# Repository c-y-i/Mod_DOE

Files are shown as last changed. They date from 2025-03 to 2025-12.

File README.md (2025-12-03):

# Mod_DOE
This GitHub repository is presented as supplementary material to the paper *Co-Optimization of Design and Manufacturing Parameters for Low-Cost Robotic Actuation*, authored by Gregory M. Campbell, Yi Cao, Hannah Escritor, Zihao Zhou, and Mark Yim. 

ArXiV to be uploaded here when created.

## **Description of the file structure**:

* Root files include .pkl files of tests for design paramaters chose by taguchi array (Taguchi_test_dict, taguchi_valve_dict) and Bayesian Optimization (BayzOp_test_dict, BO_valve_dict_High_lglg). It also includes the optimizations (BayZop_Running & BayZop_Valve) with associated utility functions (utils). It also includes the experimental scripts (Run_Gear_Experiment, Run_Valve_Experiment) with associated utility functions (Experiment_Utils). Finally, it includes .csv files of design parameters for Taguchi generated (Tag_d_params, valve_tag_d_params) and BO generated (d_params, valve_BO_d_params).

* BO_desings includes BO output design values for gear testing.

* Valve_designs includes BO output design values for valve testing.

* wolfrom includes theoretical gear design files used for parameter selection.

* CAD includes computer-aided design files for an example gear and valve mold

## Files and variables:

### **root**:

* BayZop_Running.ipynb: use Ax.dev to run Bayesian Optimization for gear parameter optimization.

* BayzOp_test_dict.pkl: 'pickle' file containing a dictionary of characterization test data for gear designs generated via Bayesian Optimization. Each 'key' contains design number: 'BO_##'. Each 'value' contains a list of [n] elements where each element represents a test. Each test element is a list of [2] elements, where each element represents a data stream. Each data element is a [m_i,2] vector in list form, where the first column represents time [ms] and the second column represents: dynamixel MX-28 torque activation [Element 0], current (mA) [Element 1]

* BayZop_Valve.ipynb: use Ax.dev to run Bayesian Optimization for valve parameter optimization.

* BO_valve_dict_High_lglg.pkl: 'pickle' file containing a dictionary of characterization test data for valve designs generated via Bayesian Optimization. Each 'key' contains information about the pressure level and pneumatic capcitor size, as well as design number: 'Prelim_High_lglg#'. Each 'value' contains a list of [n] elements where each element represents a test. Each test element is a list of [2] elements, where the first element is a [m,1] vector of time values [ms] and the second element is a list corresponding to a [2,m] vector of pressure values [kPa] where the first column represents pressure in the pre-valve pneumatic capacitor and the second column represents pressure in the post-valve pneumatic capacitor.

* d_params.csv: a comma-seperated-value file containing values relevant to CAD-work for gear designs generated via L32b Taguchi array. Wolfram gear design values provided are, in order: design number, number of teeth on sun gear, number of teeth on first part of planet gears, number of teeth on second part of planet gears, number of teeth on ring gear 2, profile shift coefficient for the sun gear, profile shift coefficient for the first part of planet gears, profile shift coefficient for the second part of planet gears, profile shift coefficient for ring gear 2, carrier radii [mm], gear thickness for all gears [mm].

* Experiment_Utils.py: utility functions to aid in valve / gear test experiments.

* Figure_Plotting.ipynb: plots and data analysis relevant to paper results.

* requirements.txt: a list of Python packages required for this code-base.

* Run_Gear_Experiment: functions for user-setup and activated of automated gear testing / data collection.

* Run_Valve_Experiment: functions for user-setup and activated of automated valve testing / data collection.

* Serial_Comms.py: utility functions for serial communication with dynamixel and ESP32.

* Tag_d_params.csv: comma-seperated-value file containing design parameter values and gear ratios for gear designs generated via L32b Taguchi array. Wolfram gear design values provided are, in order: design number, 3d-printer filament, lubricant, half the number of teeth on sun gear, number of teeth on ring gear 2, profile shift coefficient for the sun gear, profile shift coefficient for ring gear 2, clearance between teeth and roots of meshing gears [m], half the gear thickness for all gears [mm], offset integer affecting teeth and profile shift coefficient for planet 1, offset integer affecting teeth and profile shift coefficient  for planet 2, gear ratio of wolfram bilateral planetary gear.

* Taguchi_test_dict.pkl: 'pickle' file containing a dictionary of characterization test data for gear designs generated via L32b Taguchi array. Each 'key' contains design number: 'Taguchi_Design_#'. Each 'value' contains a list of [n] elements where each element represents a test. Each test element is a list of [2] elements, where each element represents a data stream. Each data element is a [2xm_i] vector in list form, where the first column represents time [ms] and the second column represents: dynamixel MX-28 torque activation [Element 0], current (mA) [Element 1]

* taguchi_valve_dict.pkl: 'pickle' file containing a dictionary of characterization test data for valve designs generated via L16b Taguchi array. Each 'key' contains information about the pressure level and pneumatic capcitor size, as well as design number: 'Prelim_High_lglg#'. Each 'value' contains a list of [n] elements where each element represents a test. Each test element is a list of [2] elements, where the first element is a [m,1] vector of time values [ms] and the second element is a list corresponding to a[2,m] vector of pressure values [kPa] where the first column represents pressure in the pre-valve pneumatic capacitor and the second column represents pressure in the post-valve pneumatic capacitor.

* utils.py: utility functions to aid in valve / gear analysis and Bayesian Optimization.

* valve_BO_d_params.csv: comma-seperated-value file containing design parameter values and test results for valve designs generated via Bayesian Optimization. Design values provided are, in order: design number, material (Ecoflex/Dragonskin silicone), valve thickness [mm], valve dome height [mm], cut length for slit in silicone valve [mm], cut geometry, test result for crack pressure [kPa], test result for steady-state pressure difference [kPa].

* valve_tag_d_params.csv: comma-seperated-value file containing design parameter values for valve designs generated via L16b Taguchi array. Design values provided are, in order: design number, material (Ecoflex/Dragonskin silicone), valve thickness [mm], valve dome height [mm], cut length for slit in silicone valve [mm], cut geometry, test result for crack pressure [kPa], test result for steady-state pressure difference [kPa].

* one_shots_d_params.csv: comma-seperated-value file containing design parameter values for valve designs generated via BO trained on 0: all Taguchi trials and 1: all Taguchi and BO trials. Design values provided are, in order: design number, material (Ecoflex/Dragonskin silicone), valve thickness [mm], valve dome height [mm], cut length for slit in silicone valve [mm], cut geometry, test result for crack pressure [kPa], test result for steady-state pressure difference [kPa].

### **BO_designs**: 

* BO_d_params.csv: a comma-seperated-value file containing values relevant to CAD-work for gear designs generated via Bayesian Optimization. Wolfram gear design values provided are, in order: design number, number of teeth on sun gear, number of teeth on first part of planet gears, number of teeth on second part of planet gears, number of teeth on ring gear 2, profile shift coefficient for the sun gear, profile shift coefficient for the first part of planet gears, profile shift coefficient for the second part of planet gears, profile shift coefficient for ring gear 2, carrier radii [mm], gear thickness for all gears [mm]. 

* BO_OneShot_d_vals.csv: a comma-seperated-value file containing values relevant to CAD-work for gear design generated via Bayesian Optimization from all Taguchi tests. Wolfram gear design values provided are, in order: design number, number of teeth on sun gear, number of teeth on first part of planet gears, number of teeth on second part of planet gears, number of teeth on ring gear 2, profile shift coefficient for the sun gear, profile shift coefficient for the first part of planet gears, profile shift coefficient for the second part of planet gears, profile shift coefficient for ring gear 2, carrier radii [mm], gear thickness for all gears [mm], clearance between teeth and roots of meshing gears [m], 3d-printer filament, lubricant.

* BO_OneShot_meta_vals.csv: comma-seperated-value file containing design parameter values and gear ratios for gear designs generated via Bayesian Optimization from all Taguchi tests. Wolfram gear design values provided are, in order: design number, 3d-printer filament, lubricant, half the number of teeth on sun gear, number of teeth on ring gear 2, profile shift coefficient for the sun gear, profile shift coefficient for ring gear 2, clearance between teeth and roots of meshing gears [m], half the gear thickness for all gears [mm], offset integer affecting teeth and profile shift coefficient for planet 1, offset integer affecting teeth and profile shift coefficient for planet 2, gear ratio of wolfram bilateral planetary gear.

* trial_[XX,YY]_d_vals.csv: comma-seperated-value file containing design parameter values and gear ratios for gear designs generated via Bayesian Optimization during acquisition that yielded design numbers XX and YY. Wolfram gear design values provided are, in order: design number, 3d-printer filament, lubricant, half the number of teeth on sun gear, number of teeth on ring gear 2, profile shift coefficient for the sun gear, profile shift coefficient for ring gear 2, clearance between teeth and roots of meshing gears [m], half the gear thickness for all gears [mm], offset integer affecting teeth and profile shift coefficient for planet 1, offset integer affecting teeth and profile shift coefficient for planet 2, gear ratio of wolfram bilateral planetary gear.

### **Valve_designs**: 

* valve_trial_[X].csv: comma-seperated-value file containing design parameter values for valve designs generated via Bayesian Optimization during acquisition that yielded design number X. Design values provided are, in order: design number, material (Ecoflex/Dragonskin silicone), cut geometry, valve thickness [mm], valve dome height [mm], cut length for slit in silicone valve [mm].

### **wolfrom**

This folder contains tools, scripts, and data for Wolfrom gearbox design and optimization.

* **gear_maker** - Gear Generator add-in for Fusion 360  
  - `gear_maker.py` - Source code for the add-in.  
  - `gear_maker.manifest` - Add-in metadata file required for Fusion 360 to run the script.  

* **config.json** - Parameter definitions and value ranges for gearbox generation.  

* **design_params.py** - Alternative method for generating design parameters for the Taguchi Array.  

* **cross_reference.py** - Post-processes results from `design_params.py` to create candidate designs for the Taguchi Array.  

* **gear_optimization_visualization.ipynb** - design space visualization for choosing relevant gear parameter inputs to L32b taguchi array.
  
### **CAD**

This folder contains printable parts and assemblies for the Wolfrom gearbox (Bayesian Optimization trial **BO22**) and the valve mold set (All-trials One-Shot).

#### [`gear_BO22`](./CAD/gear_BO22) - Wolfrom gearbox (BO trial 22)
Files here provide both individual STL parts for 3D printing and full assemblies for reference/CAD transfer.

* **STL parts (ready to print)**
  - `22_sun_12_0.7513_6.stl` - sun gear  
  - `22_planet_36_0.7854_28_*.stl` - two-stage planet gear (first and second segments)  
  - `22_ring2_76_0.1686_6.stl` - ring gear 2  
  - `ring1_90_6.stl` - ring gear 1  
  - `22_carrier2_20.7_6.stl` - planet carrier  

  *Naming note:* Filenames encode trial and key parameters (e.g., tooth counts, profile shift, thickness in mm).

* **Assemblies**
  - `BO_22_Gearbox.f3d` - Fusion 360 design file for the BO22 assembly, bearing & shaft parts included.
  - `BO_22_Gearbox.step` - neutral STEP export of the same assembly for use outside Fusion.

#### [`valve_ALL_OS`](./CAD/valve_ALL_OS) - Valve (All-trials One-Shot)
Parametric solids for the “one-shot” valve mold halves:

* `ALL_OS_f.SLDPRT` - **female** (cavity) half.  
* `ALL_OS_m.SLDPRT` - **male** (protruding/core) half.

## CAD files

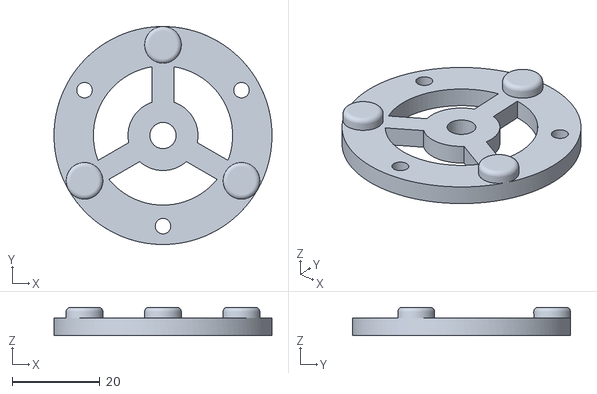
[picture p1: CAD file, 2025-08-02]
CAD/gear_BO22/22_carrier1_20.7_6.stl
49.8 x 49.8 x 6.50

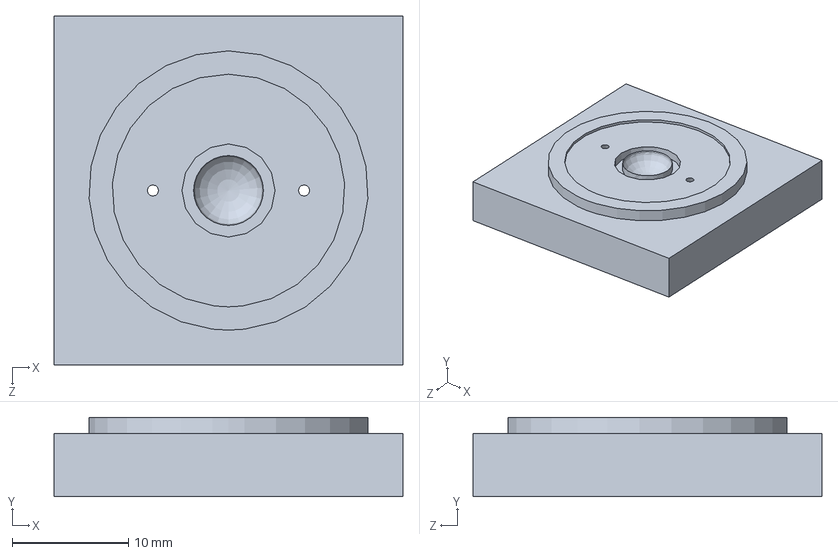
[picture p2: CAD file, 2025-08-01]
CAD/valve_ALL_OS/ALL_OS_f.SLDPRT
30.0 x 6.80 x 30.0 mm

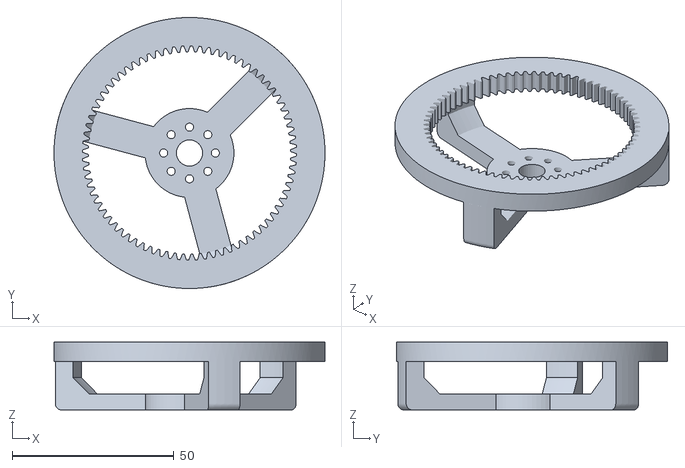
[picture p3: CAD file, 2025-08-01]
CAD/gear_BO22/22_ring2_76_0.1686_6.stl
83.8 x 83.8 x 21.0

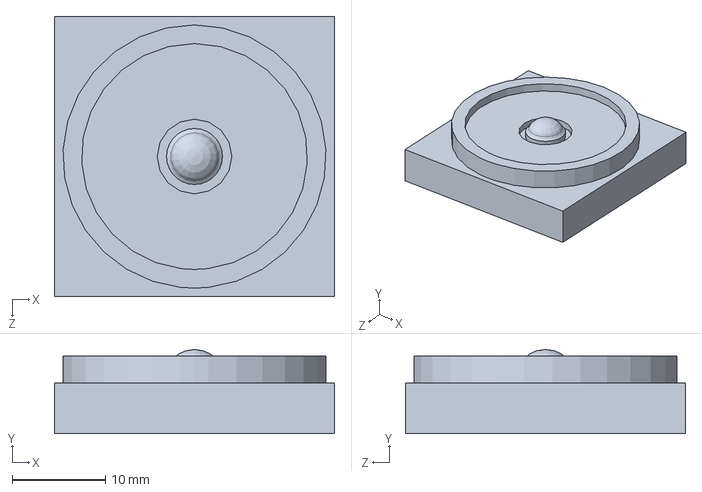
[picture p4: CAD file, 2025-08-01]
CAD/valve_ALL_OS/ALL_OS_m.SLDPRT
30.0 x 9.00 x 30.0 mm

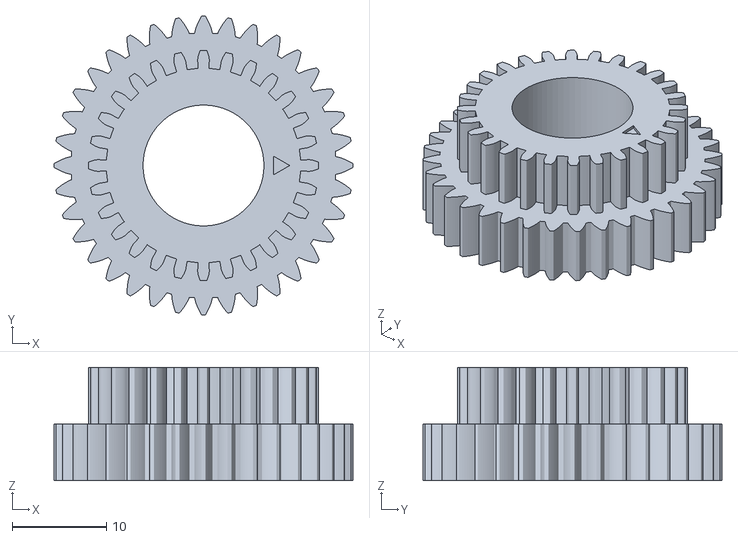
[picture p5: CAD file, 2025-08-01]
CAD/gear_BO22/22_planet_36_0.7854_28_-0.6001_6.stl
31.7 x 31.7 x 12.0

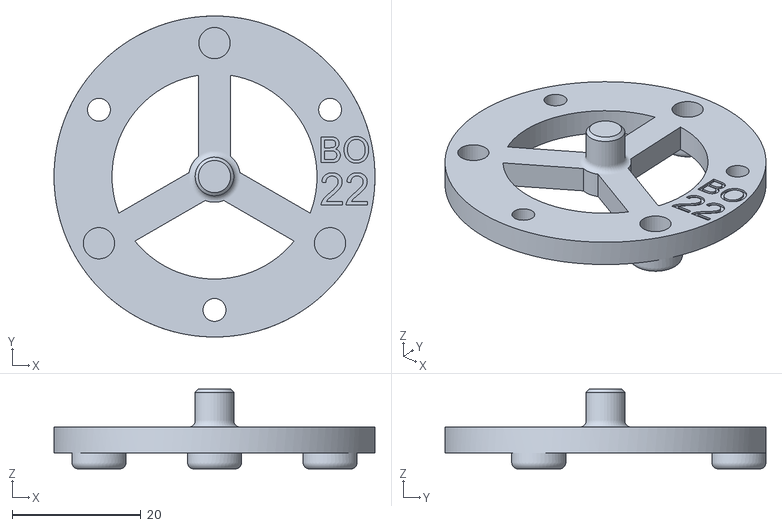
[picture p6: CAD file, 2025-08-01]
CAD/gear_BO22/22_carrier2_20.7_6.stl
49.8 x 49.8 x 12.4

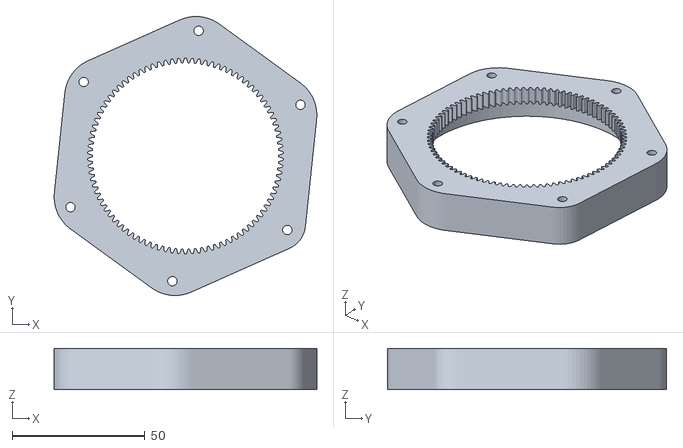
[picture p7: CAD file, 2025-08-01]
CAD/gear_BO22/ring1_90_6.stl
98.8 x 104.9 x 15.6

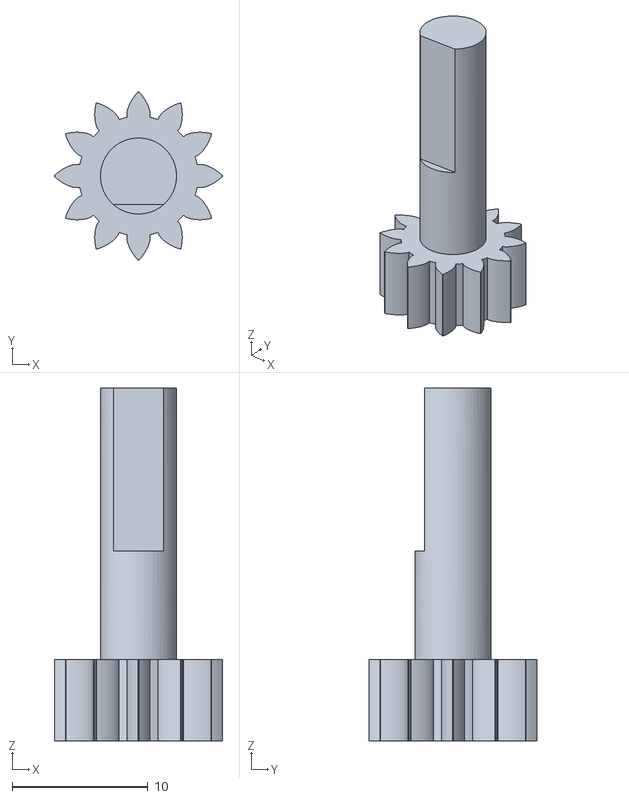
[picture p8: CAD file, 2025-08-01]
CAD/gear_BO22/22_sun_12_0.7513_6.stl
12.4 x 12.4 x 26.0

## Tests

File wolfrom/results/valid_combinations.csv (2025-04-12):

z_s | z_p1 | z_p2 | z_r2 | xs | xp1 | xp2 | xr2 | Ratio | eta_fwd | eta_bwd
10.0 | 39.0 | 29.0 | 76 | 0.6 | 0.07499999999999929 | 0.27732372741230193 | 0.8 | 83.72881355932206 | 0.6787387837036755 | 0.579254321904389
10.0 | 39.0 | 29.0 | 76 | 0.6 | 0.07499999999999929 | 0.4773237274123048 | 1.0 | 83.72881355932206 | 0.6784442759780258 | 0.5786632106196402
10.0 | 39.0 | 30.0 | 77 | 0.6 | 0.07499999999999929 | 0.27732372741230193 | 0.8 | 99.10891089108908 | 0.645448086229996 | 0.5125161415184043
10.0 | 39.0 | 30.0 | 77 | 0.6 | 0.07499999999999929 | 0.4773237274123048 | 1.0 | 99.10891089108908 | 0.64530074812077 | 0.5121894639087649
10.0 | 39.0 | 29.0 | 76 | 0.6 | 0.1999999999999993 | 0.3954293138065381 | 0.8 | 83.72881355932206 | 0.6750780789119781 | 0.568582891950358
10.0 | 39.0 | 28.0 | 75 | 0.6 | 0.07499999999999929 | 0.27732372741230193 | 0.8 | 72.22222222222224 | 0.7059739548191959 | 0.6291692645846751
10.0 | 39.0 | 28.0 | 75 | 0.6 | 0.07499999999999929 | 0.4773237274123048 | 1.0 | 72.22222222222224 | 0.7055499831154424 | 0.628381857706351
10.0 | 39.0 | 29.0 | 76 | 0.6 | 0.07499999999999929 | 0.0773237274123062 | 0.6 | 83.72881355932206 | 0.6728347683582463 | 0.567286294460555
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

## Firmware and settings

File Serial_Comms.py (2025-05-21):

"""
Created on April 28, 2024

Define variables for custom communication protocol.
Define functions for serial communications.
"""
# ~~~~~~~~~~~~~~~~~~~~~~~~~~~~~~~~~~~~~~~~~~~~~~~~~~~~~~
# imports
import serial
import time
import re

# ~~~~~~~~~~~~~~~~~~~~~~~~~~~~~~~~~~~~~~~~~~~~~~~~~~~~~~
# Commands
AIR_PUMP_ON = 'w\n'.encode()
AIR_PUMP_OFF = 's\n'.encode()
AIR_PUMP_LOW = 'e\n'.encode()

# ~~~~~~~~~~~~~~~~~~~~~~~~~~~~~~~~~~~~~~~~~~~~~~~~~~~~~~
# Function definitions

"""
Send a command (character) to the test setup via serial communications.
param serial_port: The serial port to which the test rig controller is connected.
param baud_rate: The baud rate of the serial connection.
param character: The command to be sent to the test setup.
"""
def send_character(serial_port, baud_rate=115200, character='\n'.encode(), return_error = False):
    try:
        ser = serial.Serial(serial_port, baud_rate, timeout=1)
        
        # Write the specified character to the serial line
        ser.write(character)
        # print(f"Sent {character}")
        
        # Close the serial port
        ser.close()
        
        time.sleep(0.02)

        if return_error:
            return False
        
    except serial.SerialException as e:
        print(f"An error occurred: {e}")
        if return_error:
            return True

"""
Take in a string and return a list of strings
param string: The string to be parsed.
return: A list of strings.
Note: unclear if the 'str_line[2:-3]' is necessary, but it is used in the original code. Altered for leg lifts 9/17/24.
Re Note: the -3 is to deal with '0\\n' - easier to just use values[-1] = values[-1][0]
"""
def parse_string(string, float_only = False):
    if float_only:
        matches = re.findall(r"[-+]?\d*\.\d+|\d+", string)
        float_vals = [float(match) for match in matches]
        return float_vals
    else:
        str_line = str(string.strip())
        # str_line = str_line[2:-3]
        # values = list(map(str.strip, str_line.split(',')))
        values = list(map(str.strip, str_line.split(',')))
        return values

"""
Flush the serial port buffer.
param serial_port: The serial port to which the test rig controller is connected.
param baud_rate: The baud rate of the serial connection.
"""
def flush(serial_port, baud_rate=115200):
    ser = serial.Serial(serial_port, baud_rate, bytesize=8, timeout=2, stopbits=serial.STOPBITS_ONE)
    time.sleep(0.001)
    while(ser.in_waiting > 0):
        ser.read(ser.in_waiting)
    ser.close()
    

"""
Read a string from the serial port and parse it into a list of values.
param serial_port: The serial port to which the test rig controller is connected.
param baud_rate: The baud rate of the serial connection.
return: A list of [string] values read from the serial port.
"""
def read_state(serial_port, baud_rate=115200, expected_len = 7):
    # # state = pd.DataFrame(columns=['Time','Force','Pressure','L_Height','R_Height','Flow','Limit_Switch'])
    # state = pd.DataFrame(columns=['Time','Current'])
    serialPort = serial.Serial(
        port=serial_port, baudrate=baud_rate, bytesize=8, timeout=2, stopbits=serial.STOPBITS_ONE
    )

    start_time = time.time()

    # read for at least 5ms
    while (time.time()-start_time < 0.005):

        if serialPort.in_waiting > 0:
            # Read data out of the buffer until a carraige return / new line is found
            serialString = serialPort.readline()
            # Print the contents of the serial data
            if(not serialString == b''):
                try:
                    # str_line = str(serialString)
                    values = parse_string(serialString, float_only=False)
                    if len(values) >= expected_len:
                        serialPort.close()
                        # flush(serial_port, baud_rate)
                        return values
                    else:
                        #try 1 more time
                        serialString = serialPort.readline()
                        # str_line = str(serialString)
                        values = parse_string(serialString)
                        # flush(serial_port, baud_rate)
                        serialPort.close()
                        return values
                except:
                    pass
    return 0 # if failed.


"""
Read the height from the serial port for a specified amount of time.
param read_time: The amount of time to read the height from the serial port (seconds)
param serial_port: The serial port to which the test rig controller is connected.
param baud_rate: The baud rate of the serial connection.
param max_recordable_height: The maximum height that can be recorded by the ToF sensor (must be less than error val of 999).
return: [float] The average height of the left and right ToF sensors over the specified time period (transformed via affine transform).
"""
def read_state_for(read_time, serial_port, baud_rate=115200, expected_len = 7):
    # print('Reading height for ' + str(read_time) + ' seconds')
    start_time = time.time()
    inputs = []
    serialPort = serial.Serial(
        port=serial_port, baudrate=baud_rate, bytesize=8, timeout=2, stopbits=serial.STOPBITS_ONE
    )
    time.sleep(0.005)

    # read the serial port for x seconds
    try:
        while (time.time()-start_time < read_time):
            # Wait until there is data waiting in the serial buffer
            if serialPort.in_waiting > 0:
                # Read data out of the buffer until a carraige return / new line is found
                serialString = serialPort.readline()
                # Print the contents of the serial data
                if(not serialString == b''):
                    try:
                        str_line = str(serialString)
                        values = parse_string(str_line)
                        if len(values) >= expected_len:
                            inputs.append(values)
                    except:
                        pass
    except KeyboardInterrupt:
        print('Stopped by user')

    serialPort.close()

    return inputs
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

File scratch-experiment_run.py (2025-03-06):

#!/usr/bin/env python
# -*- coding: utf-8 -*-

################################################################################
# Copyright 2017 ROBOTIS CO., LTD.
#
# Licensed under the Apache License, Version 2.0 (the "License");
# you may not use this file except in compliance with the License.
# You may obtain a copy of the License at
#
#     http://www.apache.org/licenses/LICENSE-2.0
#
# Unless required by applicable law or agreed to in writing, software
# distributed under the License is distributed on an "AS IS" BASIS,
# WITHOUT WARRANTIES OR CONDITIONS OF ANY KIND, either express or implied.
# See the License for the specific language governing permissions and
# limitations under the License.
################################################################################

# Author: Ryu Woon Jung (Leon)

#
# *********     Read and Write Example      *********
#
#
# Available DXL model on this example : All models using Protocol 1.0
# This example is tested with a DXL MX-28, and an USB2DYNAMIXEL
# Be sure that DXL MX properties are already set as %% ID : 1 / Baudnum : 34 (Baudrate : 57600)
#

import os

if os.name == 'nt':
    import msvcrt
    def getch():
        return msvcrt.getch().decode()
else:
    import sys, tty, termios
    fd = sys.stdin.fileno()
    old_settings = termios.tcgetattr(fd)
    def getch():
        try:
            tty.setraw(sys.stdin.fileno())
            ch = sys.stdin.read(1)
        finally:
            termios.tcsetattr(fd, termios.TCSADRAIN, old_settings)
        return ch

from dynamixel_sdk import *                    # Uses Dynamixel SDK library

import time                                    # Use some timers

# Control table address
ADDR_MX_TORQUE_ENABLE      = 24               # Control table address is different in Dynamixel model
ADDR_MX_GOAL_POSITION      = 30
ADDR_MX_PRESENT_POSITION   = 36
ADDR_MX_MOVING_SPEED       = 32
ADDR_MX_PRESENT_SPEED      = 38
ADDR_MX_PRESENT_LOAD       = 40
ADDR_MX_LED                = 25
CW_ANGLE_LIMIT             = 6
CCW_ANGLE_LIMIT            = 8


# Protocol version
PROTOCOL_VERSION            = 2.0               # See which protocol version is used in the Dynamixel

# Default setting
DXL_ID                      = 35                # Dynamixel ID : 1
BAUDRATE                    = 1000000           # Dynamixel default baudrate : 57600
DEVICENAME                  = '/dev/ttyUSB0'    # Check which port is being used on your controller
                                                # ex) Windows: "COM1"   Linux: "/dev/ttyUSB0" Mac: "/dev/tty.usbserial-*"

TORQUE_ENABLE               = 1                 # Value for enabling the torque
TORQUE_DISABLE              = 0                 # Value for disabling the torque

DXL_MINIMUM_POSITION_VALUE  = 10           # Dynamixel will rotate between this value
DXL_MAXIMUM_POSITION_VALUE  = 4000            # and this value (note that the Dynamixel would not move when the position value is out of movable range. Check e-manual about the range of the Dynamixel you use.)
DXL_MOVING_STATUS_THRESHOLD = 20                # Dynamixel moving status threshold

index = 0
dxl_goal_position = [DXL_MINIMUM_POSITION_VALUE, DXL_MAXIMUM_POSITION_VALUE]         # Goal position
SPEED = [100, 1124]
STOP = 0


# Initialize PortHandler instance
# Set the port path
# Get methods and members of PortHandlerLinux or PortHandlerWindows
portHandler = PortHandler(DEVICENAME)

# Initialize PacketHandler instance
# Set the protocol version
# Get methods and members of Protocol1PacketHandler or Protocol2PacketHandler
packetHandler = PacketHandler(PROTOCOL_VERSION)

# Open port
if portHandler.openPort():
    print("Succeeded to open the port")
else:
    print("Failed to open the port")
    print("Press any key to terminate...")
    getch()
    quit()


# Set port baudrate
if portHandler.setBaudRate(BAUDRATE):
    print("Succeeded to change the baudrate")
else:
    print("Failed to change the baudrate")
    print("Press any key to terminate...")
    getch()
    quit()

# Set CW & CCW Limit to 0 (for continuous rotation)
dxl_comm_result, dxl_error = packetHandler.write2ByteTxRx(portHandler, DXL_ID, CW_ANGLE_LIMIT, 0)
if dxl_comm_result != COMM_SUCCESS:
    print("%s" % packetHandler.getTxRxResult(dxl_comm_result))
elif dxl_error != 0:
    print("%s" % packetHandler.getRxPacketError(dxl_error))

dxl_comm_result, dxl_error = packetHandler.write2ByteTxRx(portHandler, DXL_ID, CCW_ANGLE_LIMIT, 0)
if dxl_comm_result != COMM_SUCCESS:
    print("%s" % packetHandler.getTxRxResult(dxl_comm_result))
elif dxl_error != 0:
    print("%s" % packetHandler.getRxPacketError(dxl_error))

# Enable Dynamixel Torque
dxl_comm_result, dxl_error = packetHandler.write1ByteTxRx(portHandler, DXL_ID, ADDR_MX_TORQUE_ENABLE, TORQUE_ENABLE)
if dxl_comm_result != COMM_SUCCESS:
    print("%s" % packetHandler.getTxRxResult(dxl_comm_result))
elif dxl_error != 0:
    print("%s" % packetHandler.getRxPacketError(dxl_error))
else:
    print("Dynamixel has been successfully connected")

while 1:
    print("Press any key to continue! (or press ESC to quit!)")
    if getch() == chr(0x1b):
        break

    # # Write goal position
    # dxl_comm_result, dxl_error = packetHandler.write2ByteTxRx(portHandler, DXL_ID, ADDR_MX_GOAL_POSITION, dxl_goal_position[index])
    # if dxl_comm_result != COMM_SUCCESS:
    #     print("%s" % packetHandler.getTxRxResult(dxl_comm_result))
    # elif dxl_error != 0:
    #     print("%s" % packetHandler.getRxPacketError(dxl_error))

    # Toggle LED
    dxl_comm_result, dxl_error = packetHandler.write1ByteTxRx(portHandler, DXL_ID, ADDR_MX_LED, index)
    if dxl_comm_result != COMM_SUCCESS:
        print("%s" % packetHandler.getTxRxResult(dxl_comm_result))
    elif dxl_error != 0:
        print("%s" % packetHandler.getRxPacketError(dxl_error))

    # # Write moving speed
    dxl_comm_result, dxl_error = packetHandler.write2ByteTxRx(portHandler, DXL_ID, ADDR_MX_MOVING_SPEED, SPEED[index])
    if dxl_comm_result != COMM_SUCCESS:
        print("%s" % packetHandler.getTxRxResult(dxl_comm_result))
    elif dxl_error != 0:
        print("%s" % packetHandler.getRxPacketError(dxl_error))

    # Write goal velocity
    # dxl_comm_result = packetHandler.write2ByteTxRx(portHandler, DXL_ID, ADDR_MX_MOVING_SPEED, 0.5)
    # if dxl_comm_result != COMM_SUCCESS:
    #     print("%s" % packetHandler.getTxRxResult(dxl_comm_result))
    # elif dxl_error != 0:
    #     print("%s" % packetHandler.getRxPacketError(dxl_error))

    # set a timer
    
    start = time.time()

    while 1:
        # Read present position
        dxl_present_position, dxl_comm_result, dxl_error = packetHandler.read2ByteTxRx(portHandler, DXL_ID, ADDR_MX_PRESENT_POSITION)
        dxl_present_speed, dxl_comm_result, dxl_error = packetHandler.read2ByteTxRx(portHandler, DXL_ID, ADDR_MX_PRESENT_SPEED)
        dxl_present_load, dxl_comm_result, dxl_error = packetHandler.read2ByteTxRx(portHandler, DXL_ID, ADDR_MX_PRESENT_LOAD)
        if dxl_comm_result != COMM_SUCCESS:
            print("%s" % packetHandler.getTxRxResult(dxl_comm_result))
        elif dxl_error != 0:
            print("%s" % packetHandler.getRxPacketError(dxl_error))

        # print("[ID:%03d] GoalPos:%03d  PresPos:%03d" % (DXL_ID, dxl_goal_position[index], dxl_present_position))
        print("[ID:%03d] PresPos:%03d, PresSpeed:%03d, PresLoad:%03d" % (DXL_ID, dxl_present_position, dxl_present_speed, dxl_present_load))

        # if not abs(dxl_goal_position[index] - dxl_present_position) > DXL_MOVING_STATUS_THRESHOLD:
        if time.time() - start > 3:
            break

    # Stop the motor
    dxl_comm_result, dxl_error = packetHandler.write2ByteTxRx(portHandler, DXL_ID, ADDR_MX_MOVING_SPEED, STOP)
    if dxl_comm_result != COMM_SUCCESS:
        print("%s" % packetHandler.getTxRxResult(dxl_comm_result))
    elif dxl_error != 0:
        print("%s" % packetHandler.getRxPacketError(dxl_error))

    # Change goal position
    if index == 0:
        index = 1
    else:
        index = 0


# Disable Dynamixel Torque
dxl_comm_result, dxl_error = packetHandler.write1ByteTxRx(portHandler, DXL_ID, ADDR_MX_TORQUE_ENABLE, TORQUE_DISABLE)
if dxl_comm_result != COMM_SUCCESS:
    print("%s" % packetHandler.getTxRxResult(dxl_comm_result))
elif dxl_error != 0:
    print("%s" % packetHandler.getRxPacketError(dxl_error))

# Close port
portHandler.closePort()

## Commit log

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2025-03-06 Implemented communication to Dynamixel & current sensor. Organized initial dictionary.
2025-03-07 Update to the analysis code.
    Added:
    - Python port of the MATLAB gear search code
    Changed:
    - Rewrote the Gearbox class using the profile shift coefficient instead of the profile shift factor equations and.
    - Added test function in gearbox.py for quick validation.
    - Updated wolfrom_analysis code to include the profile shift coefficient in the gearbox class.
    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
2025-03-30 updated cleaned design param
    [valid_combinations.csv]
2025-03-31 updated script to output full results to CSV
    [valid_combinations.csv]
2025-04-01 cross reference code, still need some work.
    [full.csv, valid_combinations.csv, valid_k_4.csv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]
2025-04-02 tuned results
    [full.csv, valid_combinations.csv, valid_k_4.csv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]
2025-04-03 Fixed cross reference logic: - Run cross_reference.py to see the candidates for Taguchi Array!
    [filtered_valid_rows.csv, valid_combinations.csv, valid_k_4.csv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]
2025-04-03 hand tuned parameter range in config, finer steps too now the results make more sense.
    [filtered_valid_rows.csv, valid_combinations.csv]
2025-04-03 updated config
    [filtered_valid_rows.csv, valid_combinations.csv, valid_k_4.csv]
2025-04-08 taguchi array params
    [filtered_valid_rows.csv, valid_combinations.csv]
2025-04-08 beginning of update towards clearance inclusion.
    [utils.py]
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2025-04-10 Now using gear-ratio based scoring (dropped using paper parameters).
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2025-04-12 - Codebase clean up, moved some code into "outdated" folder. - Updated design_params.py with updated equations from utils. - Added the efficiency plotting function to utils, design_params calls it at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
    [filtered_valid_rows.csv, valid_combinations.csv]
2025-04-14 add .csv write for AGRESSIVE parameters
    [d_params.csv, test_params_mu0.08.csv]
2025-04-14 Params for AGGRESSIVE Taguchi
    [d_params.csv]
2025-04-15 Update for resolution.
    [d_params.csv, test_params_mu0.21.csv]
2025-04-17 Curent sensing not working on Python side.
    [Run_Experiment-scratch.py, Serial_Comms.py]
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2025-04-29 Updated for cracking valve without a membrane in the loop.
2025-04-30 Error exceptions for testing
    [Experiment_Utils.py, Serial_Comms.py]
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2025-04-30 Valve sim efforts.
    [test_params_mu0.08.csv]
2025-05-06 added combine test data with metadata.
    [Tag_d_params.csv]
2025-05-06 Pulling test data to initialize Bayesian Optimization.
    [Tag_d_params.csv]
2025-05-15 Added design output to BayzOP. Next step, add experiment result read-in.
    [trial_[10, 11]_d_vals.csv]
2025-05-16 Functioning combination of experimental script with Bayesian Optimization for Human-in-the-loop testing.
    [DELETE_BO_d_params.csv]
2025-05-16 No longer changes in_vals.
    [utils.py]
2025-05-17 Running Bayesian optimization cleaned for approachability.
    [BO_d_params.csv]
2025-05-17 Generated BO 12-13
    [BO_d_params.csv, trial_[12, 13]_d_vals.csv]
2025-05-20 Generate 16_17
    [BO_d_params.csv, trial_[16, 17]_d_vals.csv]
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2025-05-21 Generated BO 18-19
    [BO_d_params.csv, trial_[18, 19]_d_vals.csv]
2025-05-21 Bayesian Optimization for Valve,
    Also added functions in utils for valve.
    TODO: Need `valve_d_params.csv` for experiments.
    [Valve_d_params.csv]
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2025-05-22 Solved BO 20&21
    [BO_d_params.csv, trial_[20, 21]_d_vals.csv]
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2025-05-28 BayzOp 22 and 23, design 24 and 25
    [BO_d_params.csv, trial_[24, 25]_d_vals.csv]
2025-05-28 BO one-shot with ALL Taguchi data
    [BO_OneShot_d_vals.csv, BO_OneShot_meta_vals.csv]
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2025-06-03 Valve BO complete for fake values. To be updated once sufficient number of Taguchi values completed.
    [Valve_d_params.csv]
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2025-06-06 Valves 4 and 8 saved as 4.1 and 8.1. Oddly only cracked under low, not high
2025-06-09 First-pass valve BO. Manual check on experimental results. 'Standard' Ax model used.
    [BO_OneShot_d_vals.csv, BO_OneShot_meta_vals.csv, valve_BO_d_params.csv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]
2025-06-10 Valve BO 5.
    [Valve_d_params.csv, valve_BO_d_params.csv, valve_tag_d_params.csv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]
2025-06-12 Design for BO 26-27
    [BO_d_params.csv, trial_[26, 27]_d_vals.csv]
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2025-06-17 BO 28-29
    [BO_d_params.csv, trial_[28, 29]_d_vals.csv]
2025-06-17 valve first BO
    [valve_BO_d_params.csv, valve_tag_d_params.csv, valve_trial_[5].csv]
2025-06-23 BO 30-31 designs
    [BO_d_params.csv, trial_[30, 31]_d_vals.csv]
2025-06-26 Veirified valve test values.
    [valve_tag_d_params.csv]
2025-06-27 Updated Taguchi Valve
    [valve_tag_d_params.csv]
2025-06-27 Bayz Op 1
    [valve_BO_d_params.csv]
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2025-07-07 BO results update - final one-shot.
    [BO_d_params.csv]
2025-07-07 File organization
    [test_params_mu0.08.csv, test_params_mu0.21.csv]
2025-07-07 ReadMe and Organization.
    [DELETE_BO_d_params.csv]
2025-07-09 New code
    [valve_BO_d_params.csv, valve_trial_[8].csv]
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2025-07-16 New Code and 567 BO Params
    [valve_BO_d_params.csv, valve_trial_[11].csv]
2025-07-16 Gear data analysis and figure generation.
    [BO_All_OneShot_d_vals.csv, BO_All_OneShot_meta_vals.csv, BO_d_params.csv]
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2025-07-17 Updated BO8
    [valve_BO_d_params.csv]
2025-07-21 Error and uncertainty for valve system.
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2025-07-22 Updated to reflect OS values used in study.
    [BO_OneShot_d_vals.csv, BO_OneShot_meta_vals.csv]
2025-07-25 Params Final
    [valve_BO_d_params.csv, valve_trial_[17].csv]
2025-07-29 All-data BO
    [valve_BO_d_params.csv]
2025-07-31 New One Shot CSV
    [one_shots_d_params.csv]
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2025-08-01 TAG OS (2)
    [one_shots_d_params.csv]
2025-08-01 Taguchi as 0, all as 1
    [one_shots_d_params.csv]
2025-08-01 CAD files for gearbox and valve mold Updated Readme for wolfrom folder.
    [22_carrier2_20.7_6.stl, 22_planet_36_0.7854_28_-0.6001_6.stl, 22_ring2_76_0.1686_6.stl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]
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2025-08-02 missing carrier1 STL for BO22
    file uploaded
    [22_carrier1_20.7_6.stl]
